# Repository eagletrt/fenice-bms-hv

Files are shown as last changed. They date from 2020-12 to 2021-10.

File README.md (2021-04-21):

# Fenice BMS - hardware

## Libraries
The projects don't include the libraries since they use the KiCAD official ones.
Set accordingly the variables `${KICAD_SYMBOL_DIR}` and `${KISYSMOD}` for 
`kicad-symbols` and `kicad-footprints` respectively.
**For `kicad-symbols` checkout the repo to `v5` for now to have the legacy ones.**

Don't rescue symbols!

## Repo structure
```
fenice-bms-hv:hw-master
|-- docs/       # Docs and datasheets of common interest
|-- mainboard/  # MainBoard hardware project folder
|-- cellboard/  # CellBoard hardware project folder
```

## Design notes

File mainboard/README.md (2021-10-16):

# MainBoard
Formula SAE - unitn

## Authors
Latest first:
- Filippo Volpe
- Franco Tabarelli
- Not clear

## Project structure
```
mainboard/
|-- MainBoard.pro           # Project file
|-- MainBoard.sch           # Schematic root
|-- MainShutdown.sch        # Analog shutdown logic schematic
|-- MCU.sch                 # MCU schematic
|-- HVSide.sch              # High voltage monitoring schematic
|-- MainBoard.kicad_pcb     # Board layout file
|-- MainBoard-cache.lib     # Local cache of symbols
|-- fp-info-cache           # Cache of footprints
|-- fp-lib-table            # List of footprint lib files
|-- sym-lib-table           # List of symbols lib files
|-- gerber/                 # Gerbers outputs
|-- netlists/               # Netlists outputs
|-- images/                 # Board renders and such
|-- docs/                   # Additional related documents and outputs
|   |-- hv-bms-mainboard.md # Report/documentation
|-- bom/                    # BOM folder
```

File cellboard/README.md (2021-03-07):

# CELLBOARD
Formula SAE - unitn

## Authors
Latest first:  
- Francesco Osti v2.1.4  
- Franco Tabarelli v2.0 - 2.1.3  
- Gregor Gombač v0 -   

## Version 2.1.4
Compared to last version we now use NTC termistor to monitor temperature and no longer use digital temperature sensors mounted on flexible PCB

## Project structure
```
cellboard
|-- CellsBoard.pro                    # Project file
|-- CellsBoard.sch                    # Cellboard main schematic
|-- PowerSupply.sch                   # Power sources schematic
|-- Balance.sch                       # Balancer schematic
|-- temperatureADC.sch                # Temperature measurement schematic
|-- Temperature section.sch           # STM microcontroller schematic
|-- LTC6813-1.sch                     # Cell voltage monitor IC schematic
|-- CellsBoard.kicad_pcb              # PCB
|-- CellsBoard-cache.lib              # Local cache of symbols        
|-- CellsBoard.net                    # Netlist
|-- CellsBoard-rescue.dcm             # Component library stuff
|-- CellsBoard-rescue.lib             # Component library stuff
|-- fp-info-cache                     # Cache of footprints
|-- fp-lib-table                      # List of footprint lib files
|-- sym-lib-table                     # List of symbols lib files
|-- modules/                          # Local symbol library files
|   |-- CellsBoard.pretty/            # Local footprint library files
|   |-- logo.kicad_mod/               # Logos fotprints
|   |-- packages3d/                   # 3D models
|   |-- simbolo_E-Agle.pretty/        # Logos E-Agle fotprints
|   |-- simbolo HV/                   # Logos HV fotprints
|-- gerber/                           # Gerber outputs
|-- library/                          # Local symbol library files
```

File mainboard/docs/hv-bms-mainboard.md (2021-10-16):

# Mainboard BMS

The goal has been creating a solid design that I hope will be carried forward with only minor adaptiations to the following team cars.

## Connections
-

## Feedbacks
What to feedback:

- SD_IN
- SD_OUT
- SD_END (no mux)
- SD_RELAY_D (no mux)
- TSAL
- AIR+_STATUS
- AIR-_STATUS
- AIR+_GATE
- AIR-_GATE
- TS_ON
- IMD_FAULT (no mux)
- IMD_LATCHED
- BMS_LATCHED
- EXT_LATCHED
- EXT_FAULT
- TS_OVER_60V_STATUS
- PRECHARGE_STATUS
- MUX_CHECK

The feedbacks are stepped down from the $12V$ logic to the $3.3V$ of the microcontroller. The signals, unless specified above, are the fed to a multiplexer CD74HC4067SM.

## TS side
### Buffers

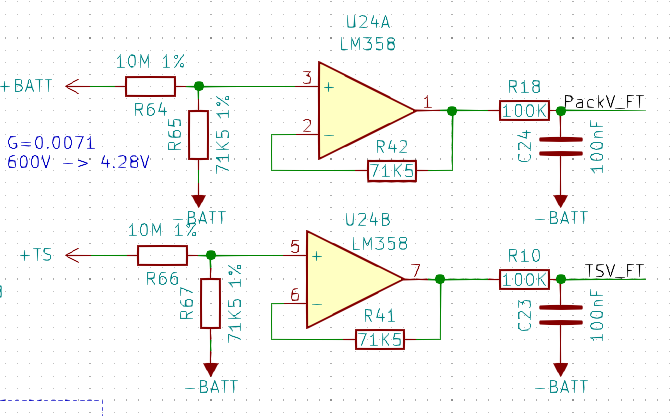
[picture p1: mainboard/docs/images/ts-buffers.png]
HV buffers


To feed the TS voltage into the ADC we use a voltage divider with the values in the image.

The OPAMP used as buffers are standard LM358, the main characteristics we are interested in are:
- Input bias current: $I_b = 45 nA$
- Output saturation voltage: $V_{OH} = V_{cc} - 1.5V = 3.5V$
The first limits the maximum value the voltage divider resistors can have, and with $R_{65} = 10M$ the current is $6uA$ at $60V$ still factor of $100$ more than $I_b$.
The second sets the maximum voltage to be buffered and in our case it's $3.2V$ at $V_{BATT} = 450V$ with some margin to limit non-linearities in the OPAMP and use an ADC at $V_{REF} = 3.3V$.

The gain is thus:
$G = \frac{R_{65}}{R_{65}+R_{64}} \approx 0.0071$

On the feedback line a resistor equal to the output impedence of the divider (hence equal to the lower resistor) is placed to remove the input bias current offset contribution at first order.

The filter cutoff frequency is:
$\omega_LP = \frac{1}{R_{18} C_{24}} = 100 rad/s \ (~16Hz)$

### ADC
Requirements:
- >= 3channels
- > 10bit
- ~ 500kbps
- Visolation > 1800V
- > 10 conversion per second
- < 10us of conversion time

The choice of the ADC was carried out taking into account the availability of the current market, previously the Si8900 IC was employed but it's no more in stock.
```{note}
The Si8900 was great because it integrated in an single package a 10bit SAR ADC and an isolation layer for the UART communication thus reducing BOM entries, space and microcontroller connections.
```

Wanting now to have a more future proof choice it has been decided to switch to a more standard configuration of separated ADC and isolation. UART devices are not common and I2C is more complex to isolate (but doable with a MAX14850). The most widespread ADCs are SPI and is simple to isolate eventhough it requires more lanes
The supply of the ADC is setted to 3.3V since the buffering OPAMP is powered from 5V and saturates.
The configuration choosen is:
- ADC124S021
	- 4 channels
	- 12bit
	- 200kbps
	- R series MUX 500Ohm
	- 50pF hold capacitance
	- 3.3V compatible

- MAX2245
- MAX2246
	- 3.3V compatible
	- 200Mbps
	- 5kV isolationwithstand

The ADC is then connected to the SPI1 on the microcontroller.

## Fan control

From TIM3_CH1 of the microcontroller put out a 25kHz PWM to control the fans.
The power for the fans is not routed to the mainboard, GND and +12V goes from the connector to the fan with a series fuse TBD on the 12V line.

## Buzzer

The buzzer is used to signal an urgency inside the TSAC.
Such emergencies are:
- Inconsistencies between control and feedbacks on the AIRs
- Prolungated overtemperature
- Fan failure

## CAN

The CAN transceiver for the communication with the outside of the TSAC is the MCP2562 which is also used in the rest of the vehicle. The termination resistor has the place to be soldered but of course it's only necessary at the end of the bus so it can be soldered in one pad only and orientated away from the other pad.

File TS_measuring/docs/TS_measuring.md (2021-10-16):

# TS_measuring

This board is meant to deal with the voltage indicator and TS voltage measuring for the TSAL control.

## Power

Power mainly comes into the board from the BMS mainboard but to comply with rule EV 5.4.10(FSG2022) it must work also when the LVS is disconnected. To achieve this a linear regulator is implemented that steps down the TS voltage to a menageable value and when the LVS is connected the regulator is for the most part disabled and power comes from the LVS for less heat production.

### Linear regulator

We opted to not use a switching regulator because the input voltage can vary an order of magnitude and would cause a regulator to be unreliable on such a wide span of possible duty cycles so a simple linear regulator is preferred.
The circuit is a classic discrete components linear regulator with the main dissipation components being a nmos DMN80H2D0SCTI capable of sustaining a Vds of 800V. The feedback works around the 0.6V of the forward bias of the base of NPN transistor Q1.

$$
	V_{out} = V_{FB} \frac{R_2+R_3}{R_3} \\
	R_2=R_3 (\frac{V_{out}-V_{FB}}{VV_{FB}})
$$

The feedback networks choice is then:
- R2 = $150k\Omega$
- R3 = $10k\Omega$

### LVS bypass

When the LVS is connected and powered the linear regulator is bypassed by the ORing and it's turned off the linreg leaving only power wasted into R1:

$$
	P_{R1,max} = \frac{(600V)^2}{R1}=0.36W
$$

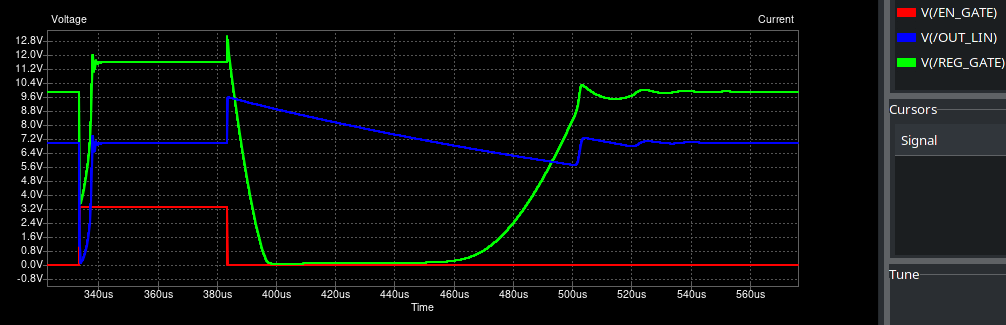
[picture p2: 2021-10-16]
TS_measuring/docs/images/output_short_regulation.png

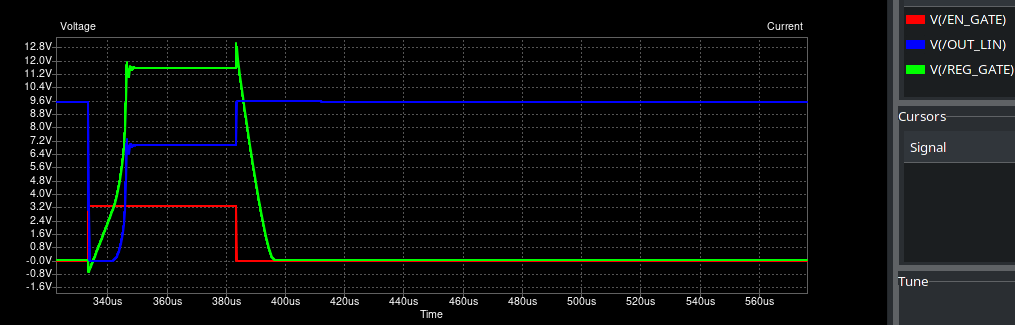
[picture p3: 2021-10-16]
TS_measuring/docs/images/output_short_to_open_regulation.png

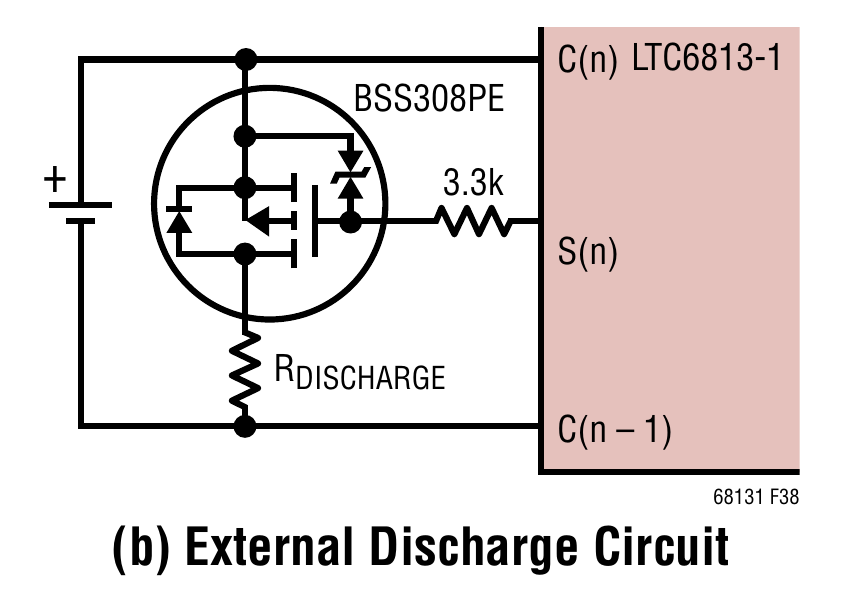
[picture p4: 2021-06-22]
cellboard/docs/images/LTC6813_cell_connection.png

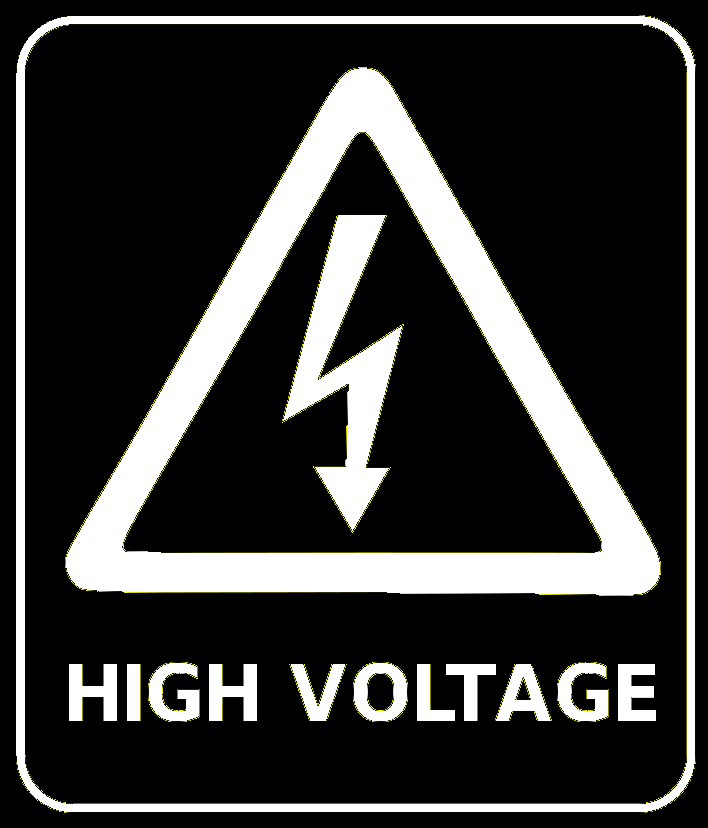
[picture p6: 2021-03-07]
cellboard/modules/simbolo HV/hv_colo.png

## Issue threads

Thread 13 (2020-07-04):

Current measurement

Bonnee, 2020-07-04:
Implement formula reading from current sensors, with some way to switch between sensors when a current threshold is reached

Bonnee, 2021-09-25:
Mostly fixed by 0509a0651be2edcbd3b963c28a7c65b585f54e12

Closed 2021-09-25.

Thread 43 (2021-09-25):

EEPROM doesn't work

Bonnee, 2021-09-25:
On the latest F4 board, communication with the on-board EEPROM is broken. It might be a driver issue, but as far as I remember the driver worked on the G4 board. @volpx please check that nothing changed on the EEPROM circuit.

volpx, 2021-10-02:
Doesn't answer to SPI commands, always returns 0xFF.

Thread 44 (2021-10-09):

ADC1 in DMA mode doesn't work

Bonnee, 2021-10-09:
Starting ADC1 in DMA mode does only one conversion and then stops. Read values seem to overflow at 255, meaning only 8 bits are used. Should not be a problem since ADC2 and ADC3 are used to measure current and the feedbacks can only be read in polling mode since they are multiplexed

volpx, 2021-10-10:
The multiplexer is not the reason the feedbacks can't be DMAed. You can probably do it but the reason is it's not necessary to have them DMAed.

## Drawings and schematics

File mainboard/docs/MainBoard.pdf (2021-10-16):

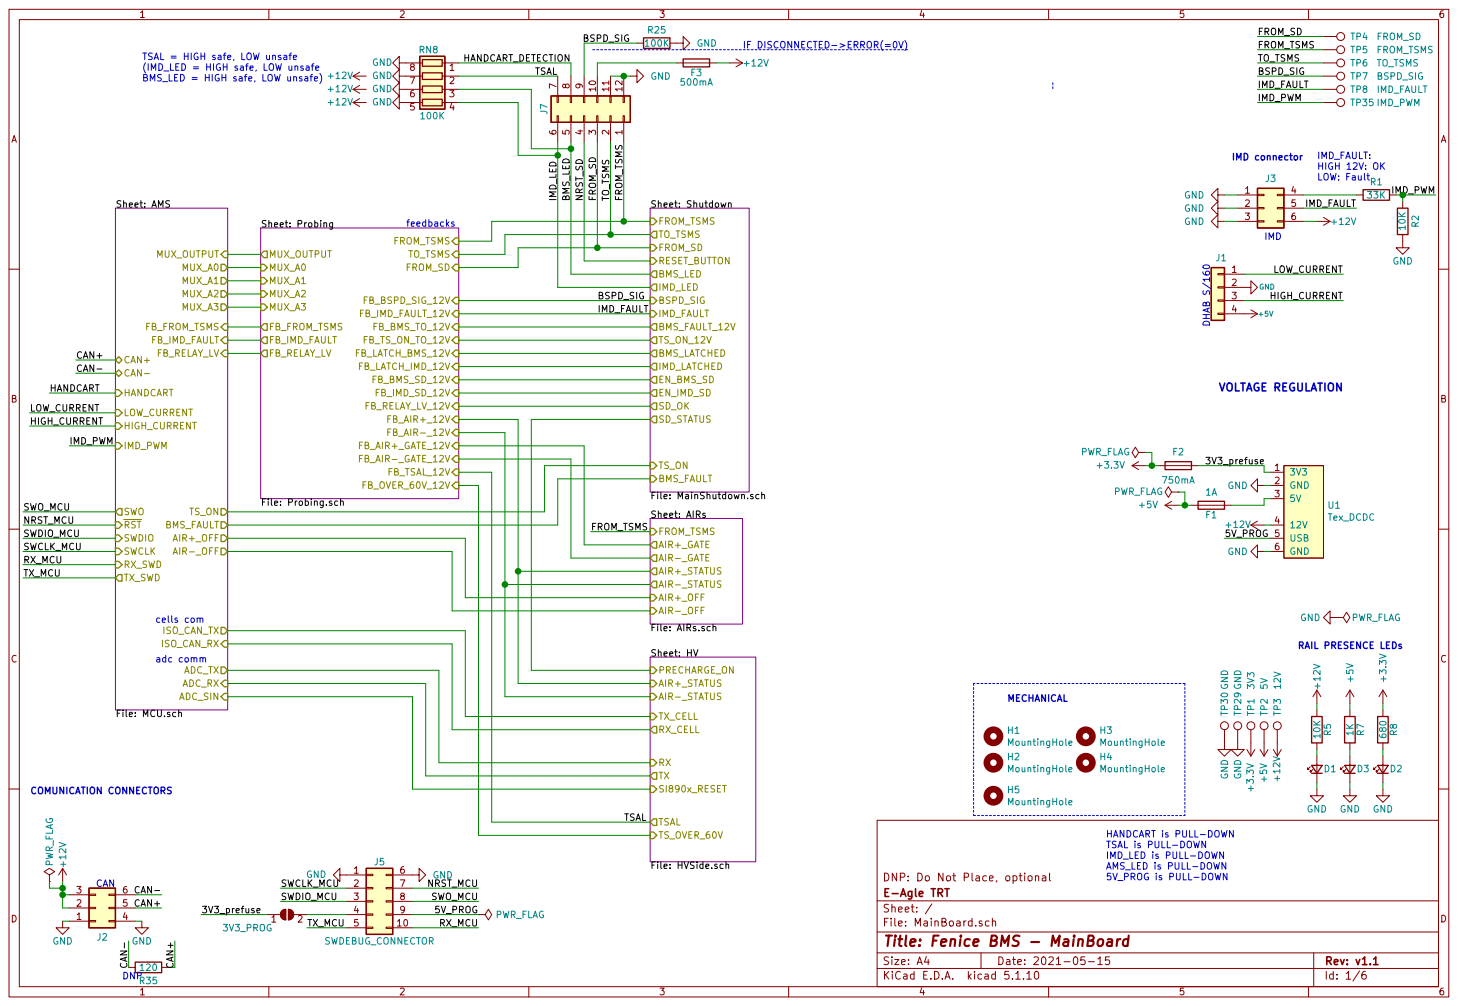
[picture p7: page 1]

LOW: Fault TSAL = HIGH safe, LOW unsafe
(IMD_LED = HIGH safe, LOW unsafe

IF DISCONNECTED->ERROR(=0V)
Sheet: Shutdown File: MainShutdown.sch TS_ON

AIR+_STATUS
AIR-_STATUS
AIR-_OFF AIR+_OFF Sheet: HV
File: HVSide.sch AIR-_STATUS
TXRX_CELL TX_CELL SI890x_RESET

TSAL is PULL-DOWN
IMD_LED is PULL-DOWN
AMS_LED is PULL-DOWN
5V_PROG is PULL-DOWN

DNP: Do Not Place, optional
File: MainBoard.sch Sheet: / E-Agle TRT

Id: 1/6 Title: Fenice BMS - MainBoard

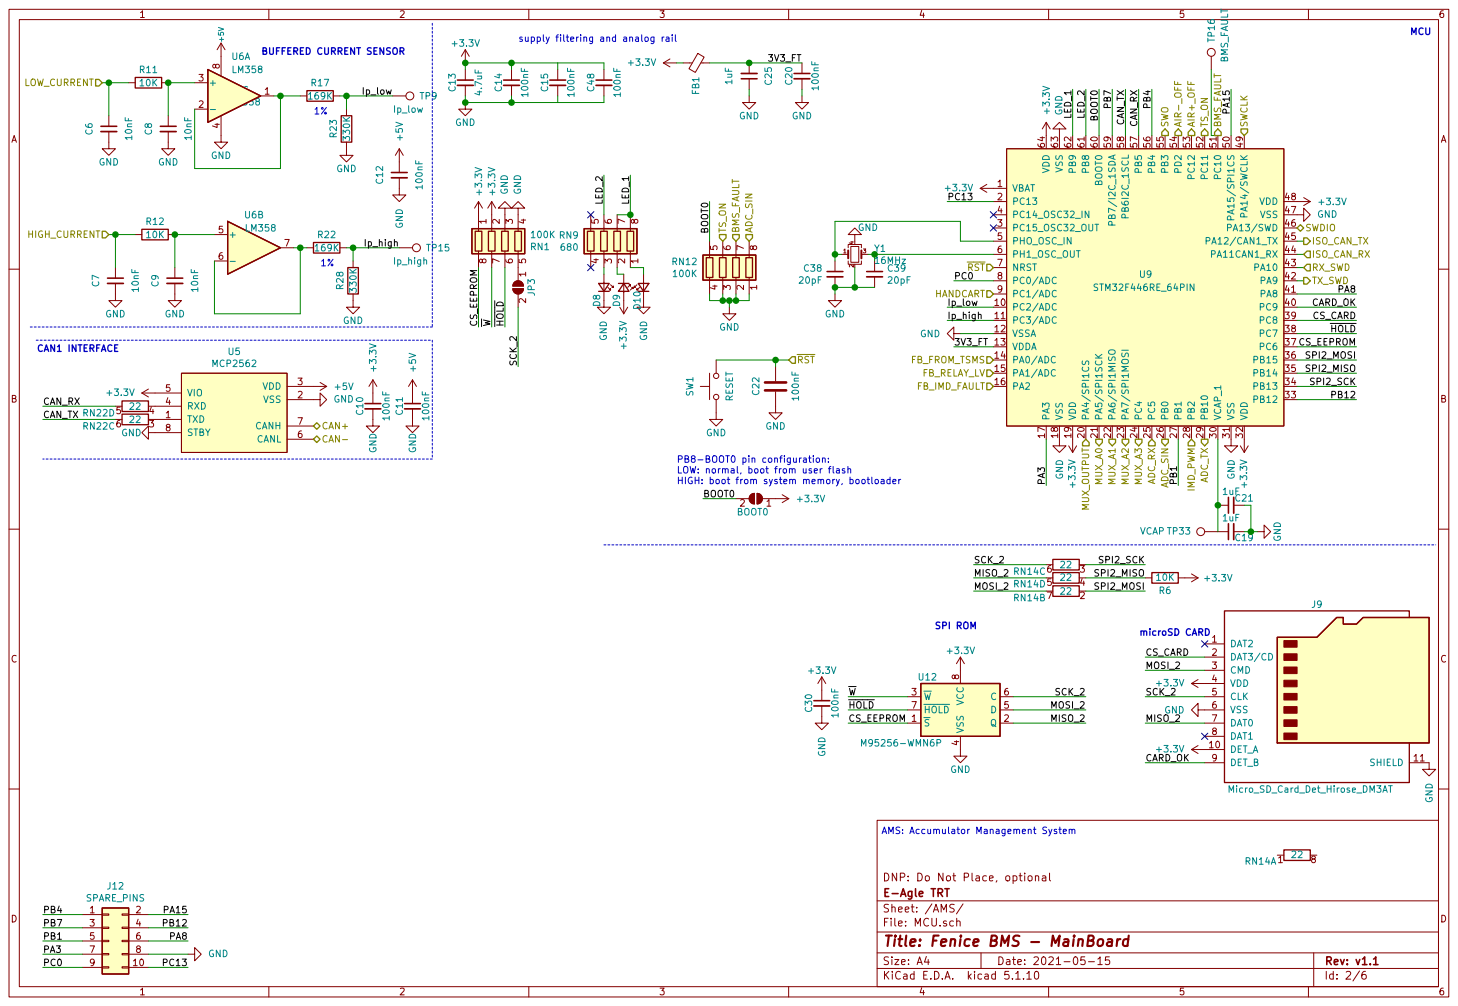
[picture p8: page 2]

supply filtering and analog rail

AMS: Accumulator Management System

DNP: Do Not Place, optional
File: MCU.sch Sheet: /AMS/ E-Agle TRT

Id: 2/6 Title: Fenice BMS - MainBoard

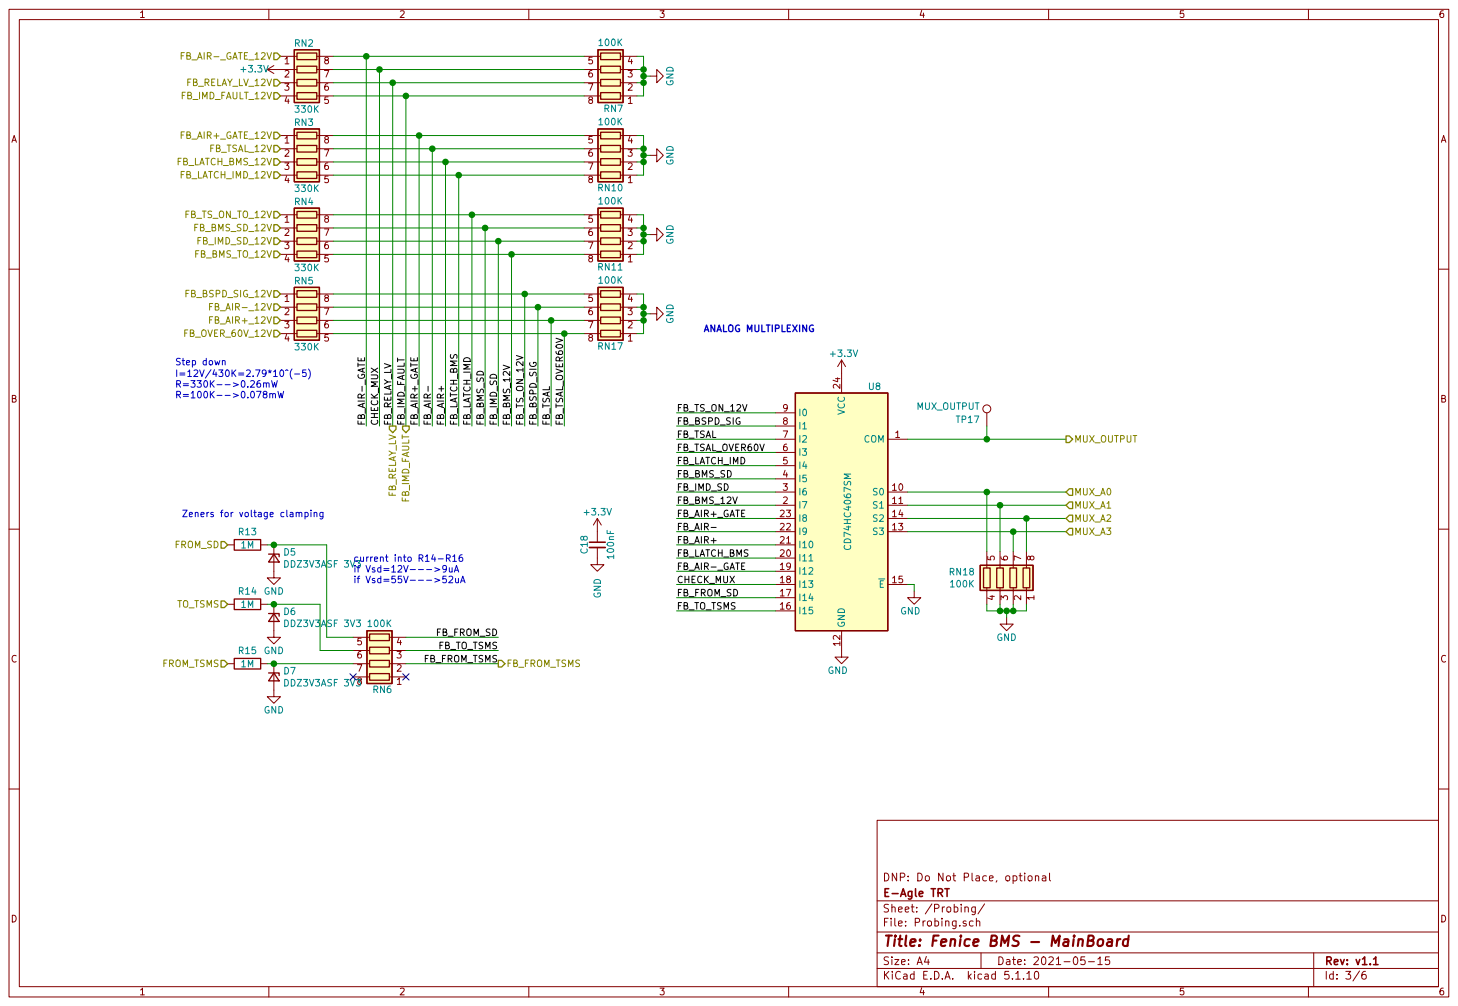
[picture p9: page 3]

Zeners for voltage clamping

DNP: Do Not Place, optional GND

E-Agle TRT
Sheet: /Probing/
File: Probing.sch
Id: 3/6 Title: Fenice BMS - MainBoard

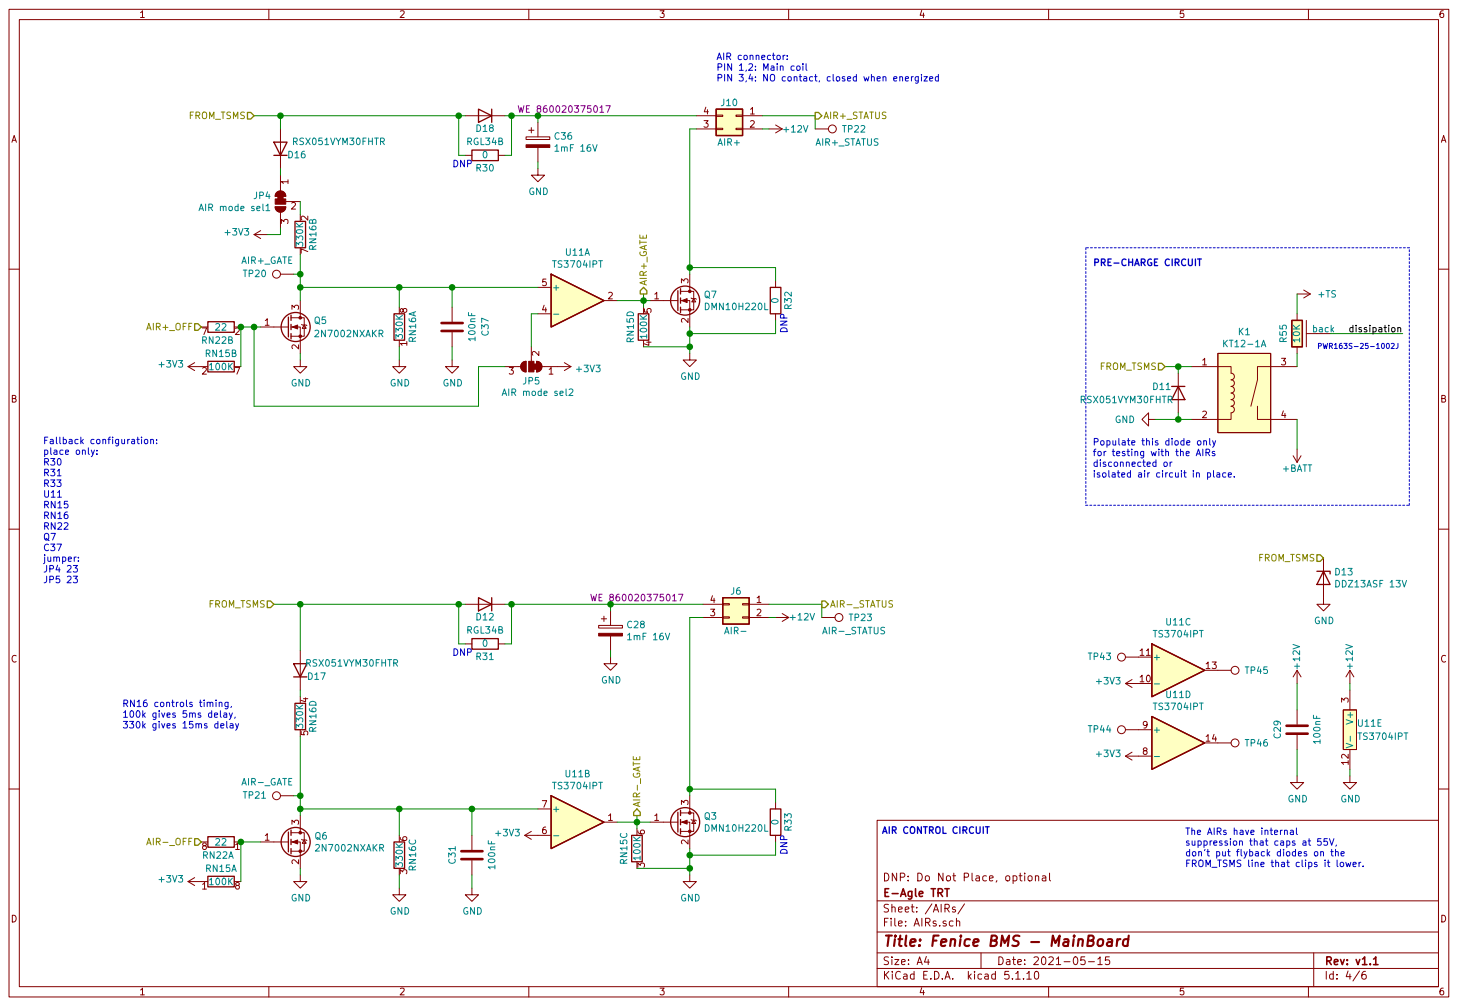
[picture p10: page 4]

AIR connector: PIN 1,2: Main coil PIN 3,4: NO contact, closed when energized

PWR163S-25-1002J Populate this diode only
FROM_TSMS

for testing with the AIRs disconnected or

isolated air circuit in place. DNP

AIR CONTROL CIRCUIT DNP

The AIRs have internal suppression that caps at 55V,

don't put flyback diodes on the
FROM_TSMS line that clips it lower.

DNP: Do Not Place, optional
File: AIRs.sch Sheet: /AIRs/ E-Agle TRT

Id: 4/6 Title: Fenice BMS - MainBoard

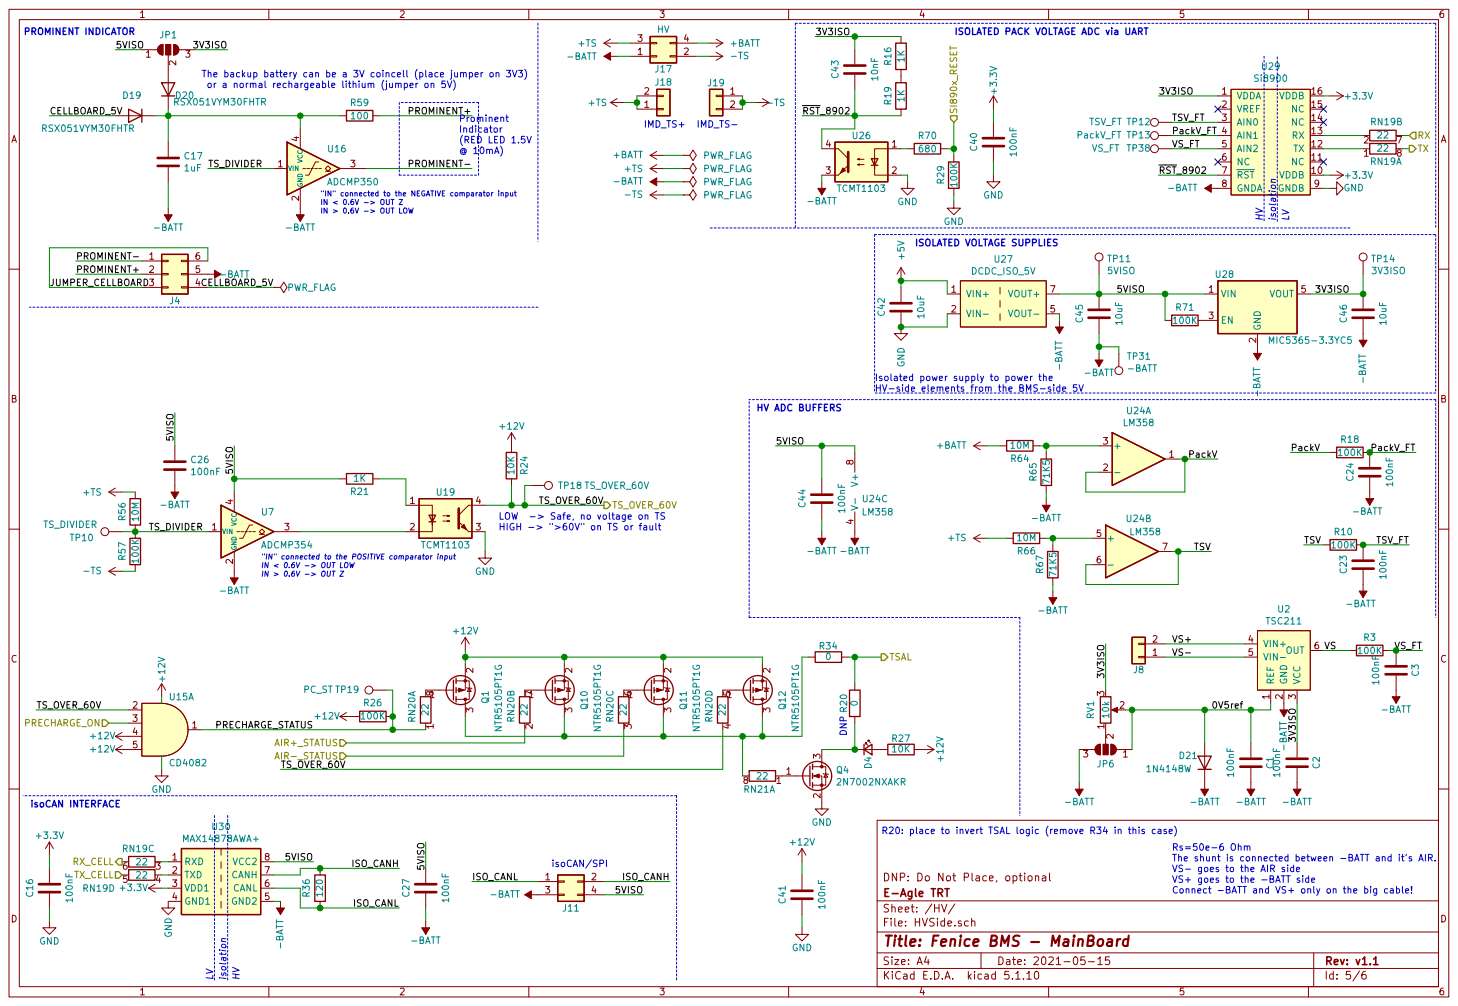
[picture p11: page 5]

3V3ISO
The backup battery can be a 3V coincell (place jumper on 3V3)
or a normal rechargeable lithium (jumper on 5V)

"IN" connected to the NEGATIVE comparator input
IN < 0.6V -> OUT Z
IN > 0.6V -> OUT LOW

LOW -> Safe, no voltage on TS HIGH -> ">60V" on TS or fault

"IN" connected to the POSITIVE comparator input
IN < 0.6V -> OUT LOW
IN > 0.6V -> OUT Z

3 VIN+ 4 VIN- 5 OUT 6 U2 TSC211 -BATT3 6 RN20C 22 C2 100nF -BATT C3 100nF -BATT C1 100nF -BATT

DNP: Do Not Place, optional R26

R20: place to invert TSAL logic (remove R34 in this case)

The shunt is connected between -BATT and it's AIR. VS- goes to the AIR side

File: HVSide.sch Sheet: /HV/ E-Agle TRT

VS+ goes to the -BATT side

Id: 5/6 Title: Fenice BMS - MainBoard

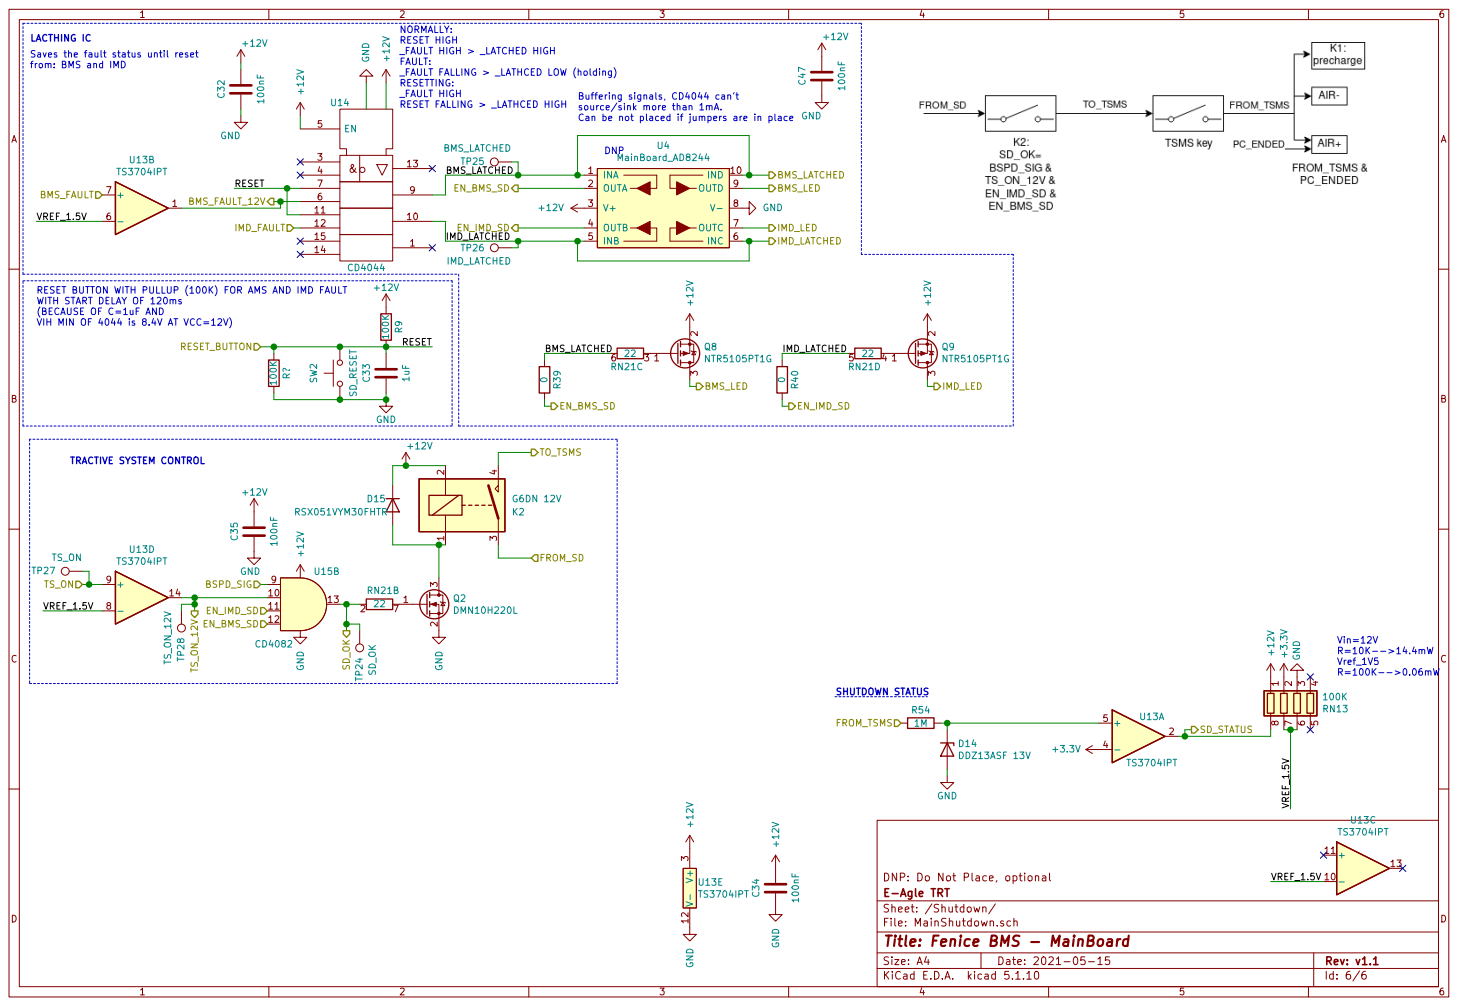
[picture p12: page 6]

LACTHING IC
Saves the fault status until reset
from: BMS and IMD

RESET NORMALLY: RESET HIGH
RESET

_FAULT HIGH > _LATCHED HIGH
FAULT: _FAULT FALLING > _LATHCED LOW (holding) RESETTING: _FAULT HIGH

Buffering signals, CD4044 can't source/sink more than 1mA. Can be not placed if jumpers are in place DNP

RESET BUTTON WITH PULLUP (100K) FOR AMS AND IMD FAULT WITH START DELAY OF 120ms (BECAUSE OF C=1uF AND

DNP: Do Not Place, optional R9 100K TP24 SD_OK +12V

VIH MIN OF 4044 is 8.4V AT VCC=12V)

File: MainShutdown.sch Sheet: /Shutdown/ E-Agle TRT

Id: 6/6 Title: Fenice BMS - MainBoard

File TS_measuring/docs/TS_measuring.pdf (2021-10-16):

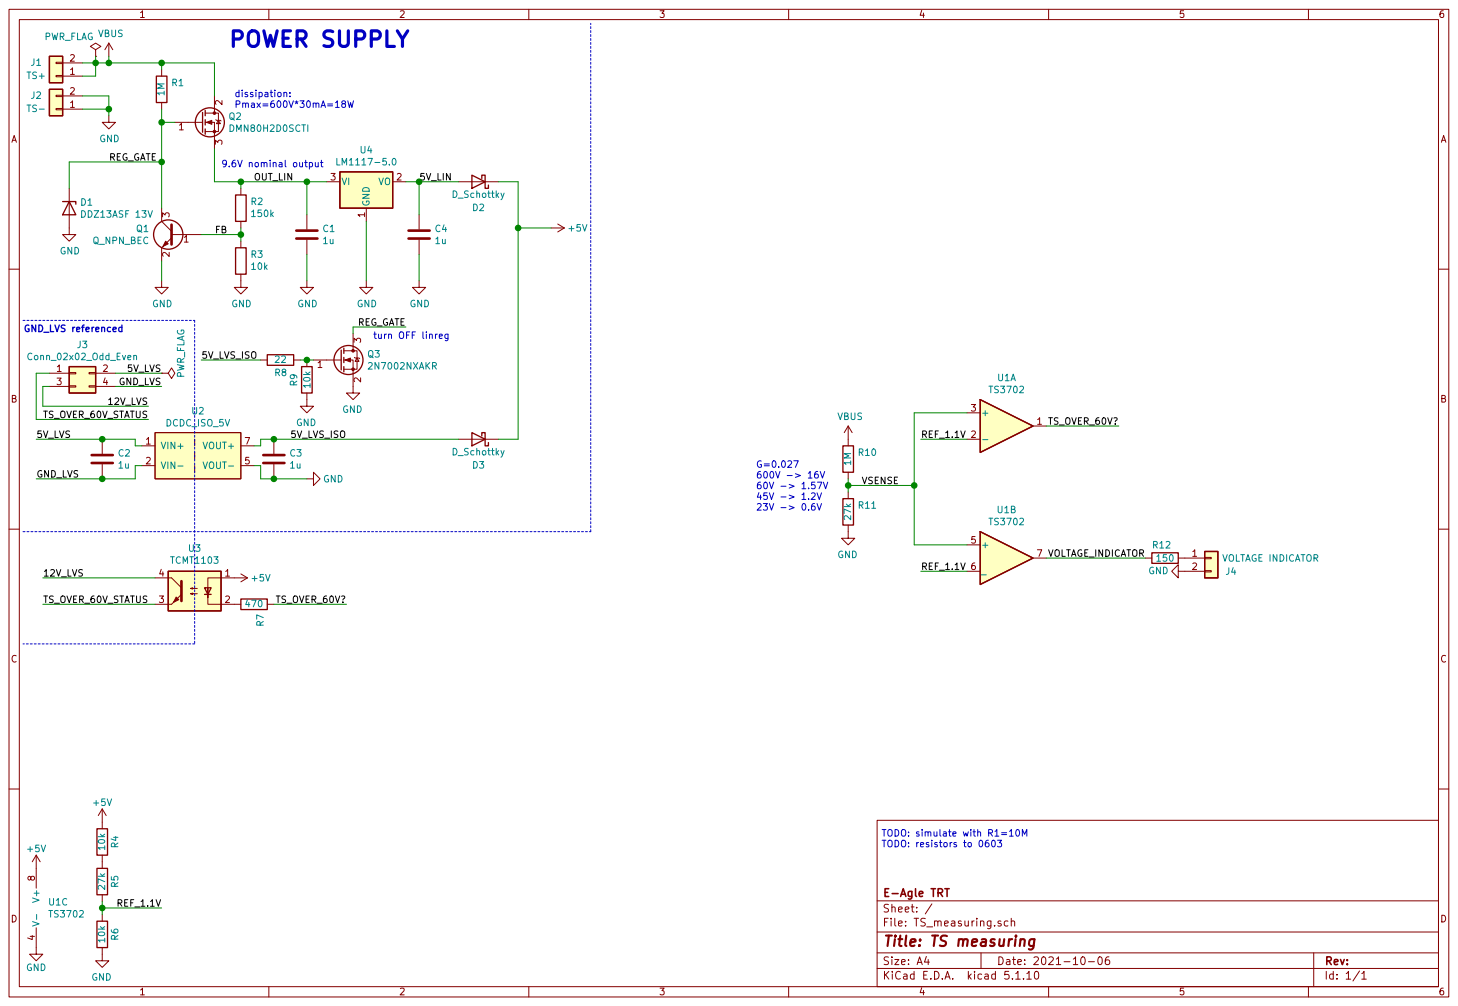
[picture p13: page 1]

File: TS_measuring.sch Sheet: / E-Agle TRT GND

Id: 1/1 Title: TS measuring

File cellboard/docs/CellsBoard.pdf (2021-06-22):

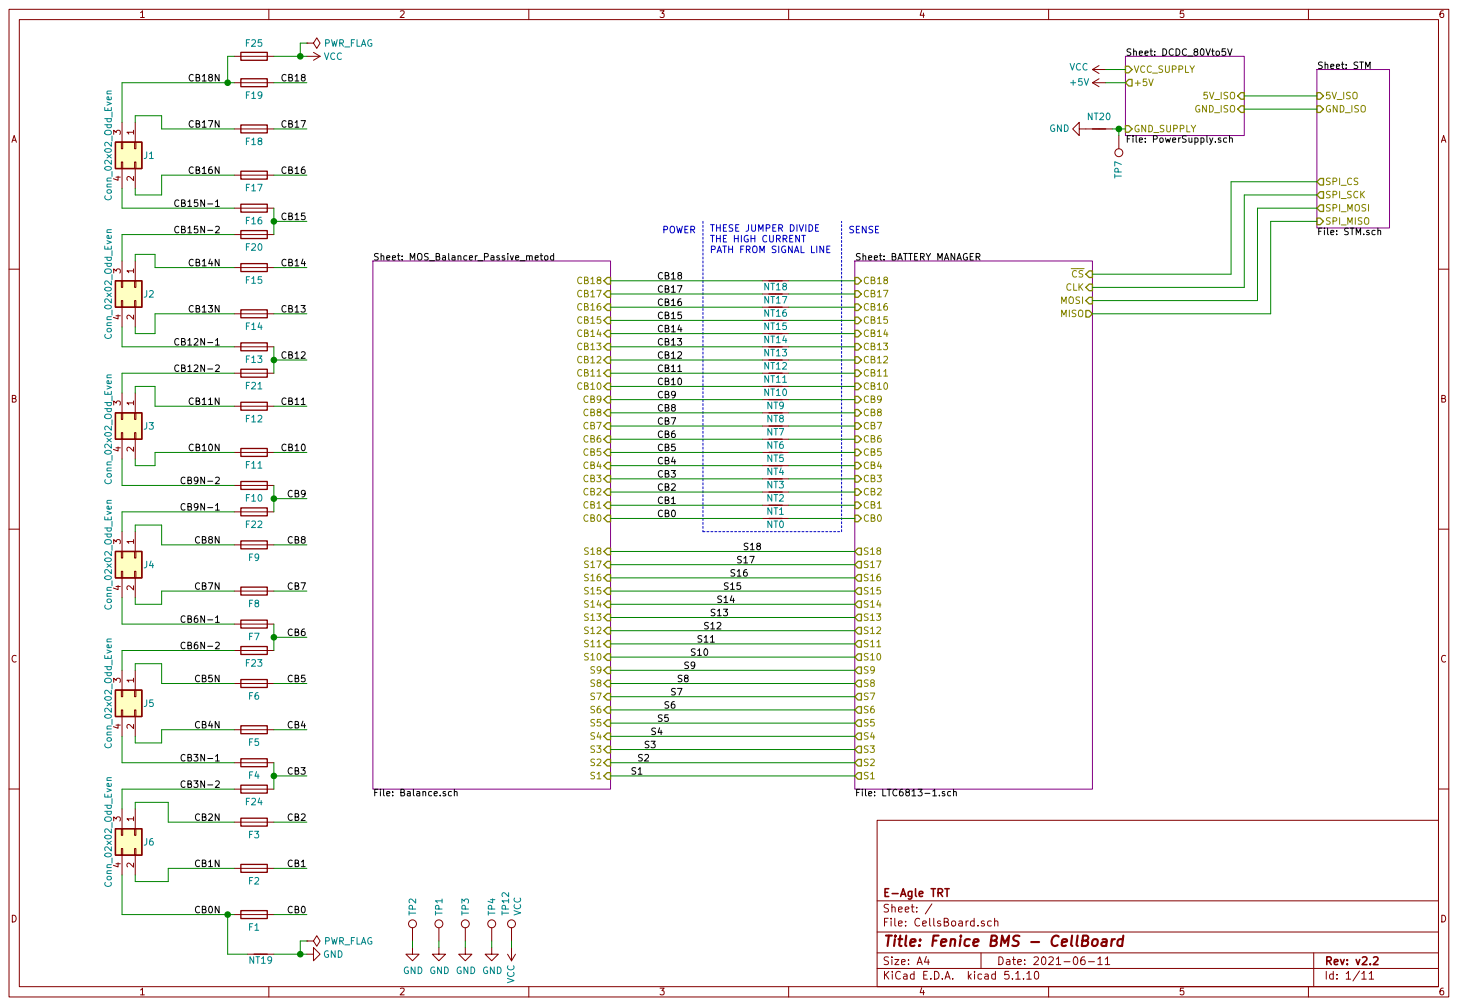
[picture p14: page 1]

THESE JUMPER DIVIDE
THE HIGH CURRENT PATH FROM SIGNAL LINE

File: CellsBoard.sch Sheet: / E-Agle TRT

Id: 1/11 Title: Fenice BMS - CellBoard

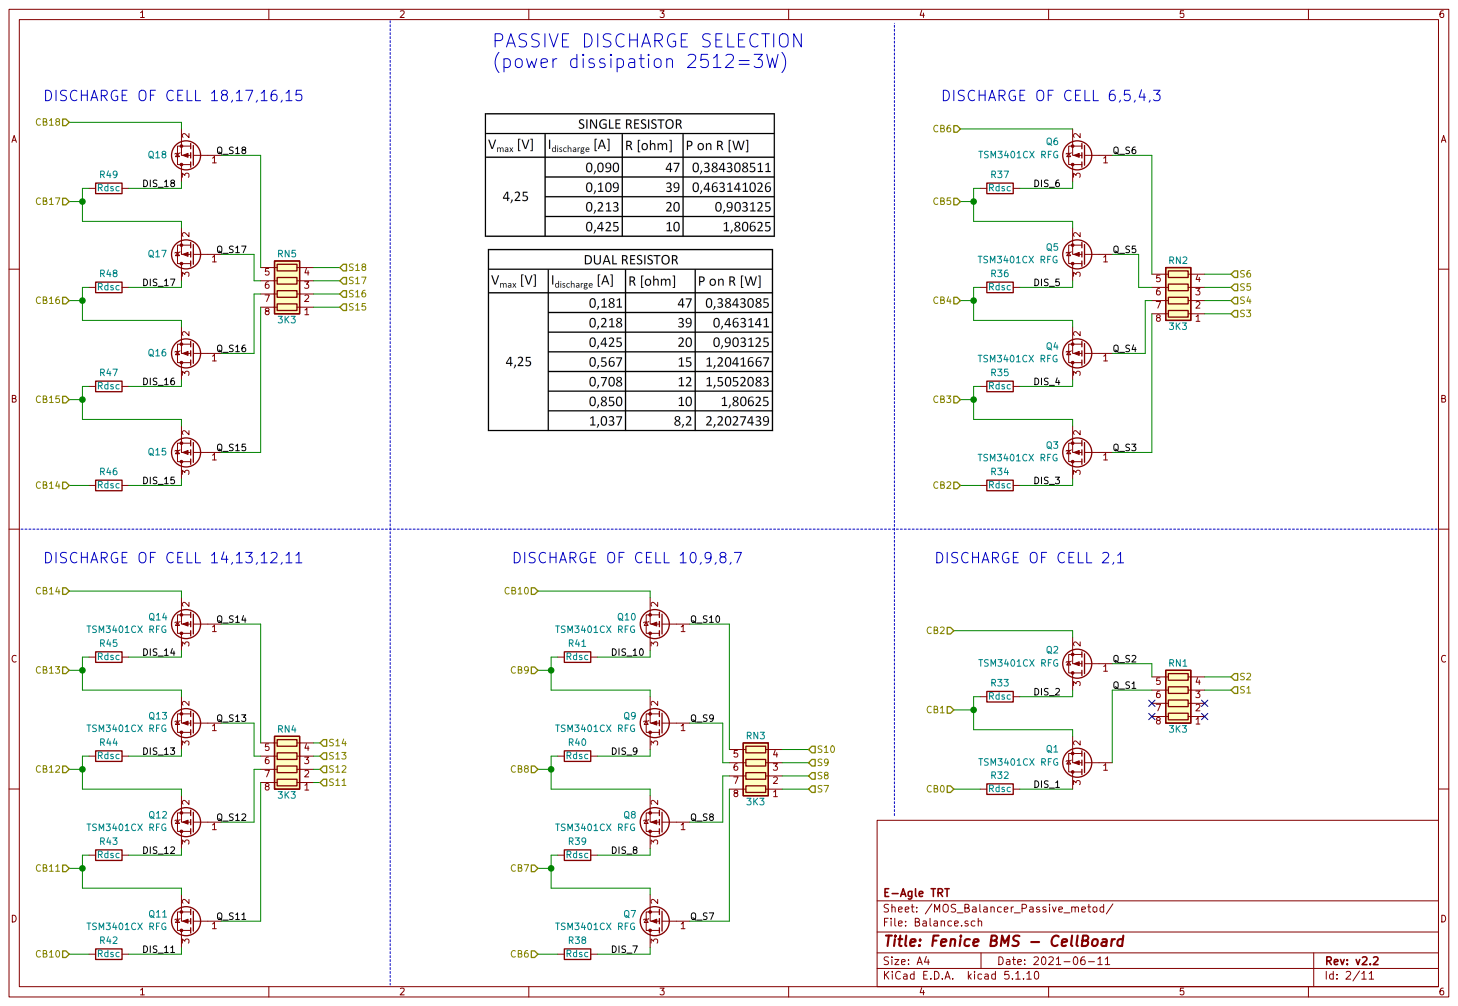
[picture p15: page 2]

E-Agle TRT
File: Balance.sch Sheet: /MOS_Balancer_Passive_metod/
Id: 2/11 Title: Fenice BMS - CellBoard

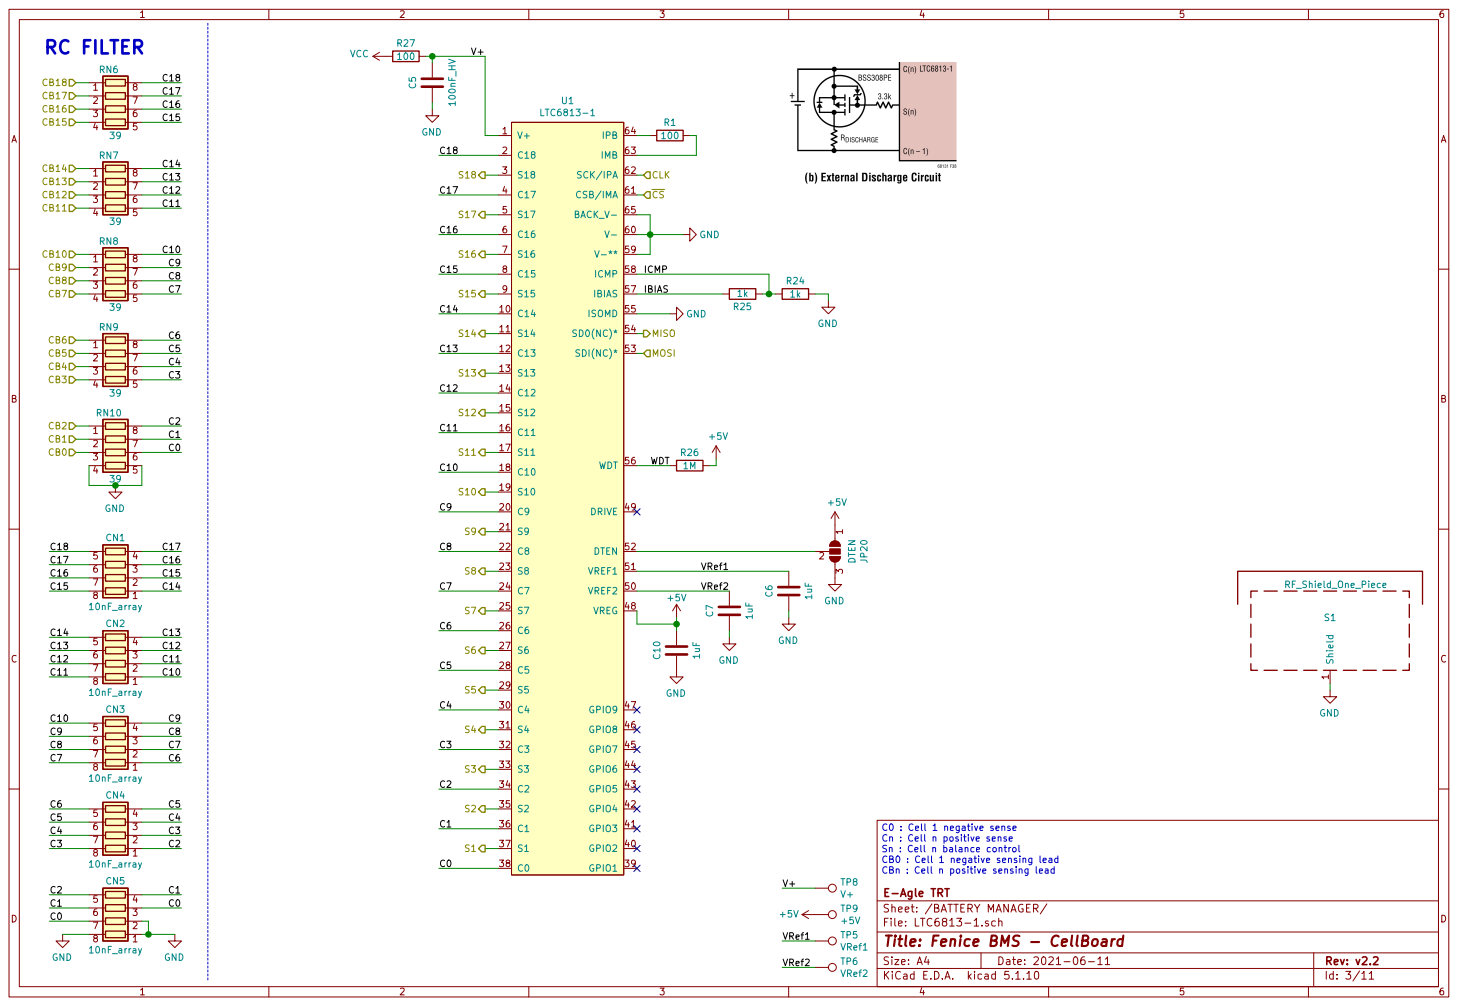
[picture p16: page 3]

C0 : Cell 1 negative sense
Cn : Cell n positive sense Sn : Cell n balance control CB0 : Cell 1 negative sensing lead

CBn : Cell n positive sensing lead

TP5 VRef1 TP6 VRef2
Id: 3/11 Title: Fenice BMS - CellBoard

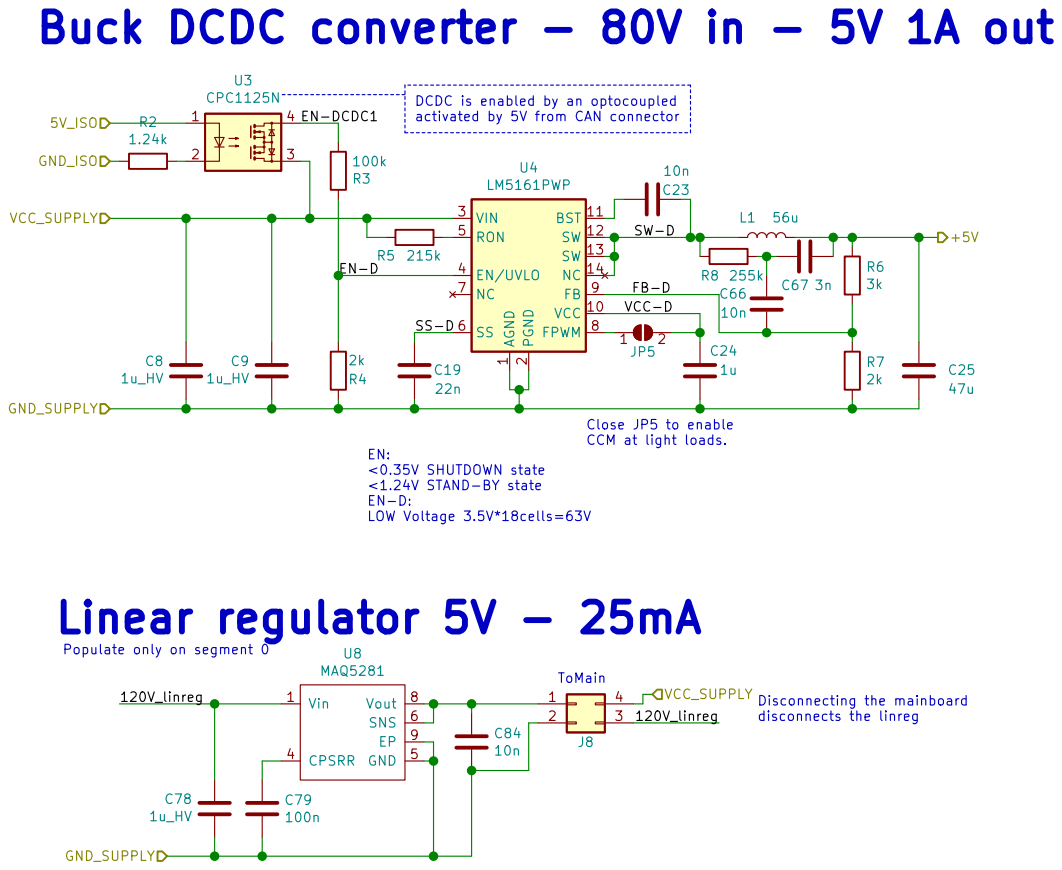
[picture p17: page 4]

Buck DCDC converter - 80V in - 5V 1A out

activated by 5V from CAN connector Close JP5 to enable CCM at light loads. ToMain Populate only on segment 0
5V_ISO

2 VIN 3 EN/UVLO 4 RON 5 SS 6 NC 7 FPWM 8 FB 9 U4
120V_linreg SW-D
10n VCC_SUPPLY

1 VCC 10 BST 11 SW 12 SW 13 NC 14 PGND

disconnects the linreg EN: <0.35V SHUTDOWN state <1.24V STAND-BY state EN-D: LOW Voltage 3.5V*18cells=63V

E-Agle TRT
Sheet: /DCDC_80Vto5V/
File: PowerSupply.sch
Id: 4/11 Title: Fenice BMS - CellBoard

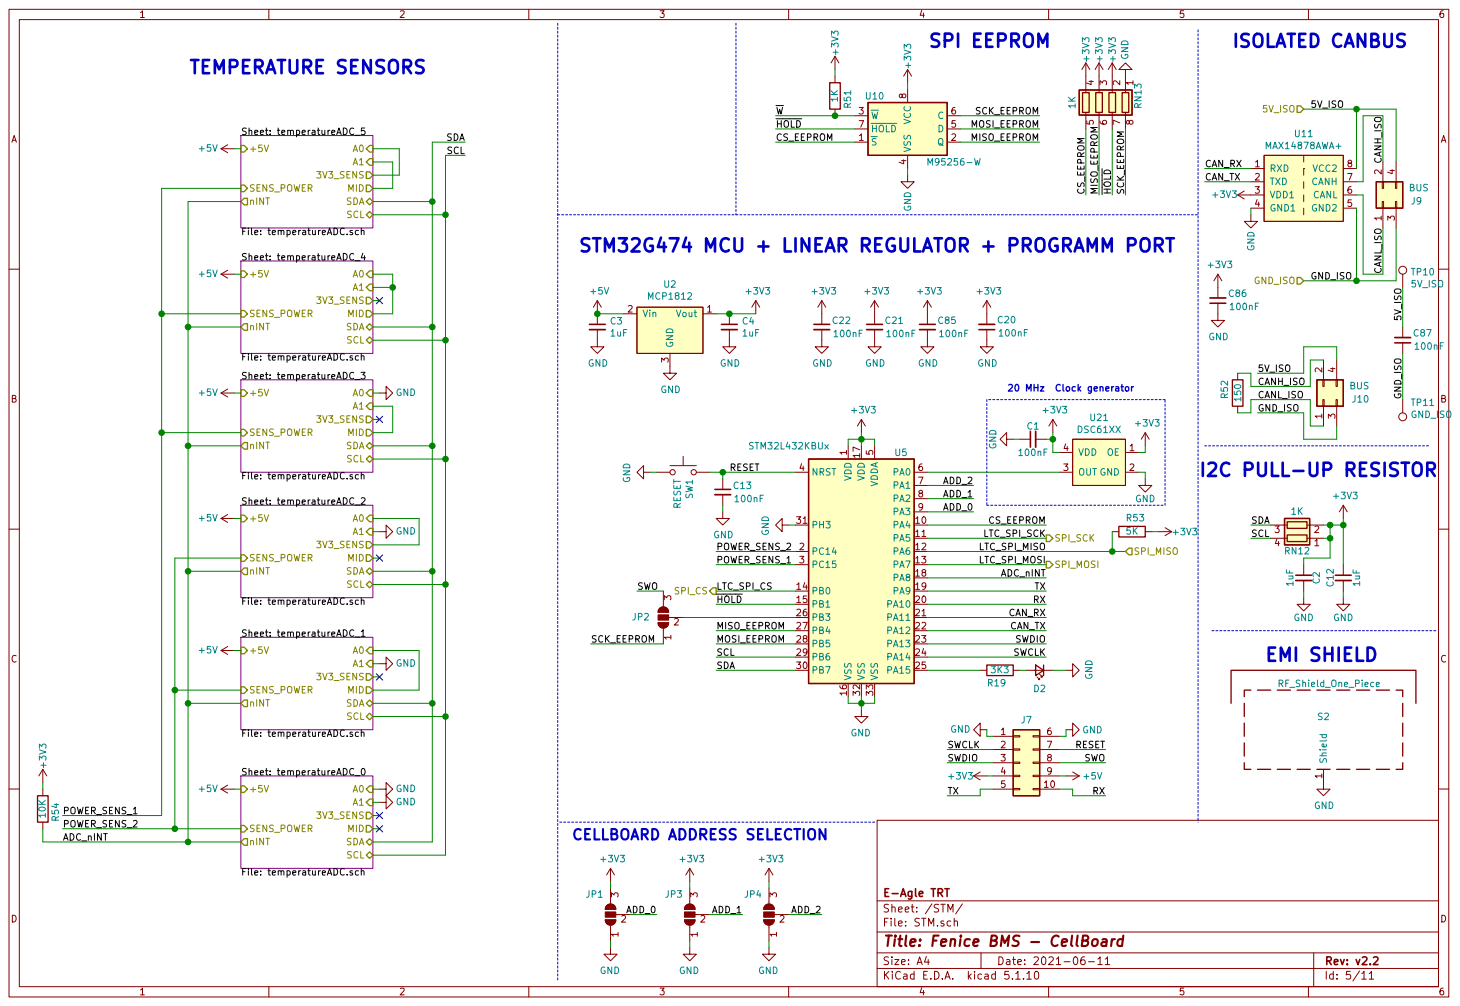
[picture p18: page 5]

STM32G474 MCU + LINEAR REGULATOR + PROGRAMM PORT

5 VSS 16 VSS 32 VSS 33 U5 STM32L432KBUx GND GND

File: STM.sch Sheet: /STM/ E-Agle TRT

Id: 5/11 Title: Fenice BMS - CellBoard


E-Agle TRT
Sheet: /STM/temperatureADC_3/
File: temperatureADC.sch
Id: 6/11 Title: Fenice BMS - CellBoard


E-Agle TRT
Sheet: /STM/temperatureADC_4/
File: temperatureADC.sch
Id: 7/11 Title: Fenice BMS - CellBoard


E-Agle TRT
Sheet: /STM/temperatureADC_1/
File: temperatureADC.sch
Id: 8/11 Title: Fenice BMS - CellBoard


E-Agle TRT
Sheet: /STM/temperatureADC_0/
File: temperatureADC.sch
Id: 9/11 Title: Fenice BMS - CellBoard


E-Agle TRT
Sheet: /STM/temperatureADC_2/
File: temperatureADC.sch
Id: 10/11 Title: Fenice BMS - CellBoard


E-Agle TRT
Sheet: /STM/temperatureADC_5/
File: temperatureADC.sch
Id: 11/11 Title: Fenice BMS - CellBoard





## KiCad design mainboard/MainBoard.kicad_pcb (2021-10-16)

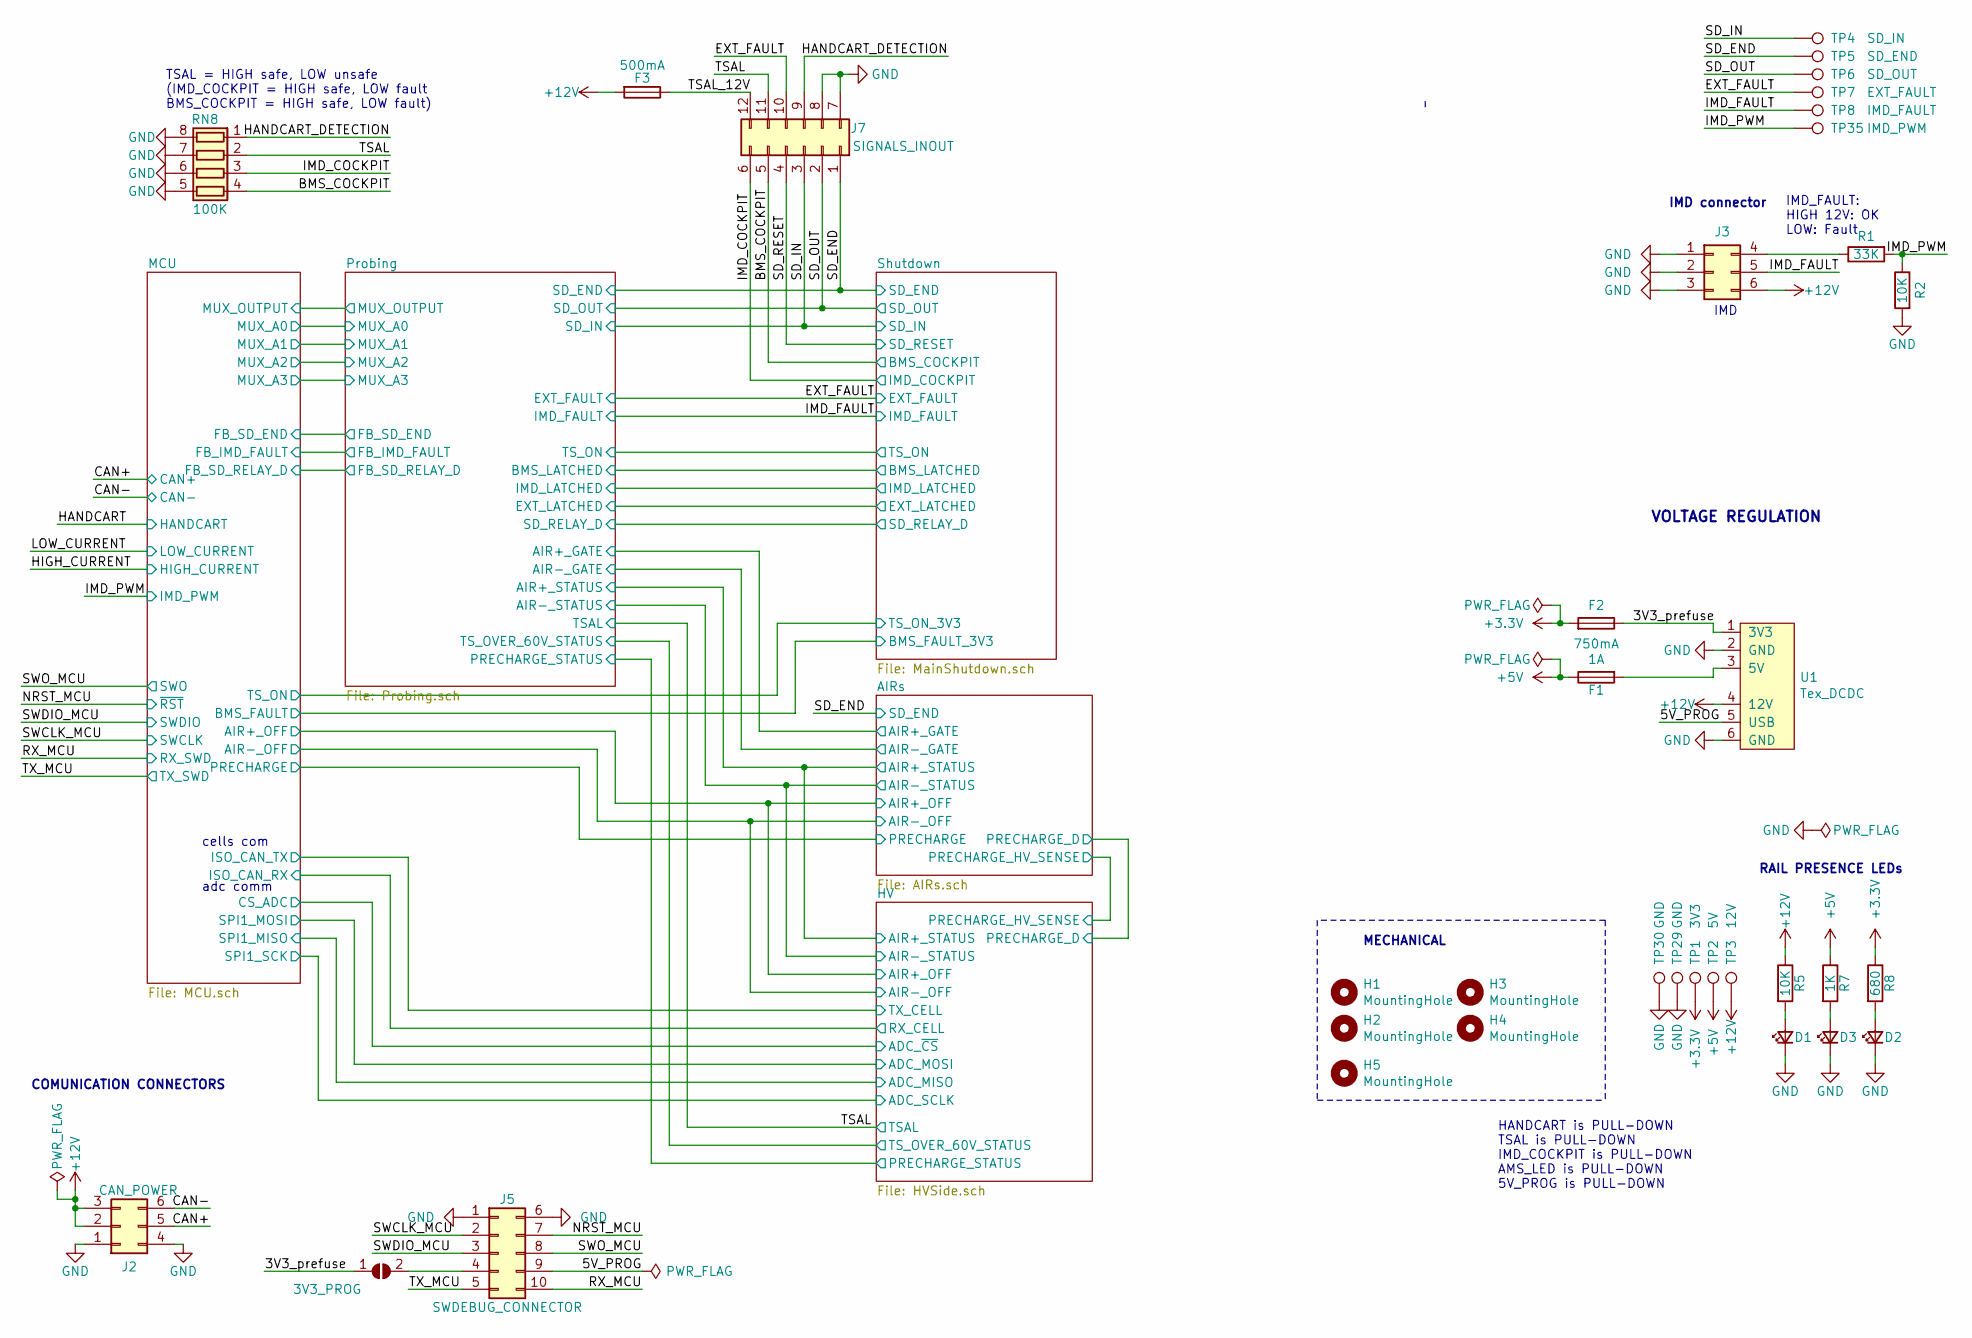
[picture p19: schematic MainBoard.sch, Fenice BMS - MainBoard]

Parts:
D1, D2, D3: LED_Small; LED_0603_1608Metric_Castellated
F1: 1A; Fuse_0805_2012Metric
F2: 750mA; Fuse_0805_2012Metric
F3: 500mA; Fuse_1812_4532Metric
H1, H2, H3, H4, H5: MountingHole; MountingHole_3.2_6.1Free
J2: CAN_POWER; Molex_Micro-Fit_3.0_43045-0612_2x03_P3.00mm_Vertical
J3: CONN_2X3; Molex_Micro-Fit_3.0_43045-0612_2x03_P3.00mm_Vertical
J5: SWDEBUG_CONNECTOR; Molex_Nano-Fit_105310-xx10_2x05_P2.50mm_Vertical
J7: SIGNALS_INOUT; Molex_Micro-Fit_3.0_43045-1212_2x06_P3.00mm_Vertical
JP2: 3V3_PROG; SolderJumper-2_P1.3mm_Open_RoundedPad1.0x1.5mm
R1: 33K; R_0603_1608Metric
R2, R5: 10K; R_0603_1608Metric
R7: 1K; R_0603_1608Metric
R8: 680; R_0603_1608Metric
RN8: 100K; R_Array_Convex_4x0603
TP1: 3V3; TestPoint_Pad_D1.0mm
TP2: 5V; TestPoint_Pad_D1.0mm
TP3: 12V; TestPoint_Pad_D1.0mm
TP4: SD_IN; TestPoint_Pad_D1.0mm
TP5: SD_END; TestPoint_Pad_D1.0mm
TP6: SD_OUT; TestPoint_Pad_D1.0mm
TP7: EXT_FAULT; TestPoint_Pad_D1.0mm
TP8: IMD_FAULT; TestPoint_Pad_D1.0mm
TP29, TP30: GND; TestPoint_GNDedge
TP35: IMD_PWM; TestPoint_Pad_D1.0mm
U1: Tex_DCDC; Tex_DCDC_vertical_up

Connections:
+5V: F1.1, R7.1, TP2.1; also elsewhere on the board
+12V: F3.2, J2.2, J2.3, J3.6, R5.1, TP3.1, U1.4 (12V); also elsewhere on the board
/3V3_prefuse: F2.1, JP2.1 (A), U1.1 (3V3)
/5V_PROG: J5.9, U1.5 (USB)
/BMS_COCKPIT: J7.5, RN8.4 (R4.1); also elsewhere on the board
/CAN+: J2.5; also elsewhere on the board
/CAN-: J2.6; also elsewhere on the board
/EXT_FAULT: J7.10, TP7.1; also elsewhere on the board
/HANDCART_DETECTION: J7.9, RN8.1 (R1.1)
/IMD_COCKPIT: J7.6, RN8.3 (R3.1); also elsewhere on the board
/IMD_FAULT: J3.5, TP8.1; also elsewhere on the board
/IMD_PWM: R1.2, R2.1, TP35.1; also elsewhere on the board
/NRST_MCU: J5.7; also elsewhere on the board
/RX_MCU: J5.10; also elsewhere on the board
/SD_END: J7.1, TP5.1; also elsewhere on the board
/SD_IN: J7.3, TP4.1; also elsewhere on the board
/SD_OUT: J7.2, TP6.1; also elsewhere on the board
/SD_RESET: J7.4; also elsewhere on the board
/SWCLK_MCU: J5.2; also elsewhere on the board
/SWDIO_MCU: J5.3; also elsewhere on the board
/SWO_MCU: J5.8; also elsewhere on the board
/TSAL: J7.11, RN8.2 (R2.1); also elsewhere on the board
/TSAL_12V: F3.1, J7.12
/TX_MCU: J5.5; also elsewhere on the board
GND: D1.1 (K), D2.1 (K), D3.1 (K), J2.1, J2.4, J3.1, J3.2, J3.3, J5.1, J5.6, J7.7, J7.8, R2.2, RN8.5 (R4.2), RN8.6 (R3.2), RN8.7 (R2.2), RN8.8 (R1.2), TP29.1, TP30.1, U1.2 (GND), U1.6 (GND); also elsewhere on the board
unnamed: D1.2 (A), R5.2
unnamed: D2.2 (A), R8.2
unnamed: D3.2 (A), R7.2
unnamed: F1.2, U1.3 (5V)
unnamed: J3.4, R1.1
unnamed: J5.4, JP2.2 (B)

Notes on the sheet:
IMD
IMD connector
COMUNICATION CONNECTORS
MECHANICAL
IMD_FAULT: HIGH 12V: OK LOW: Fault
adc comm
TSAL = HIGH safe, LOW unsafe (IMD_COCKPIT = HIGH safe, LOW fault BMS_COCKPIT = HIGH safe, LOW fault)
cells com
HANDCART is PULL-DOWN TSAL is PULL-DOWN IMD_COCKPIT is PULL-DOWN AMS_LED is PULL-DOWN 5V_PROG is PULL-DOWN
VOLTAGE REGULATION
RAIL PRESENCE LEDs

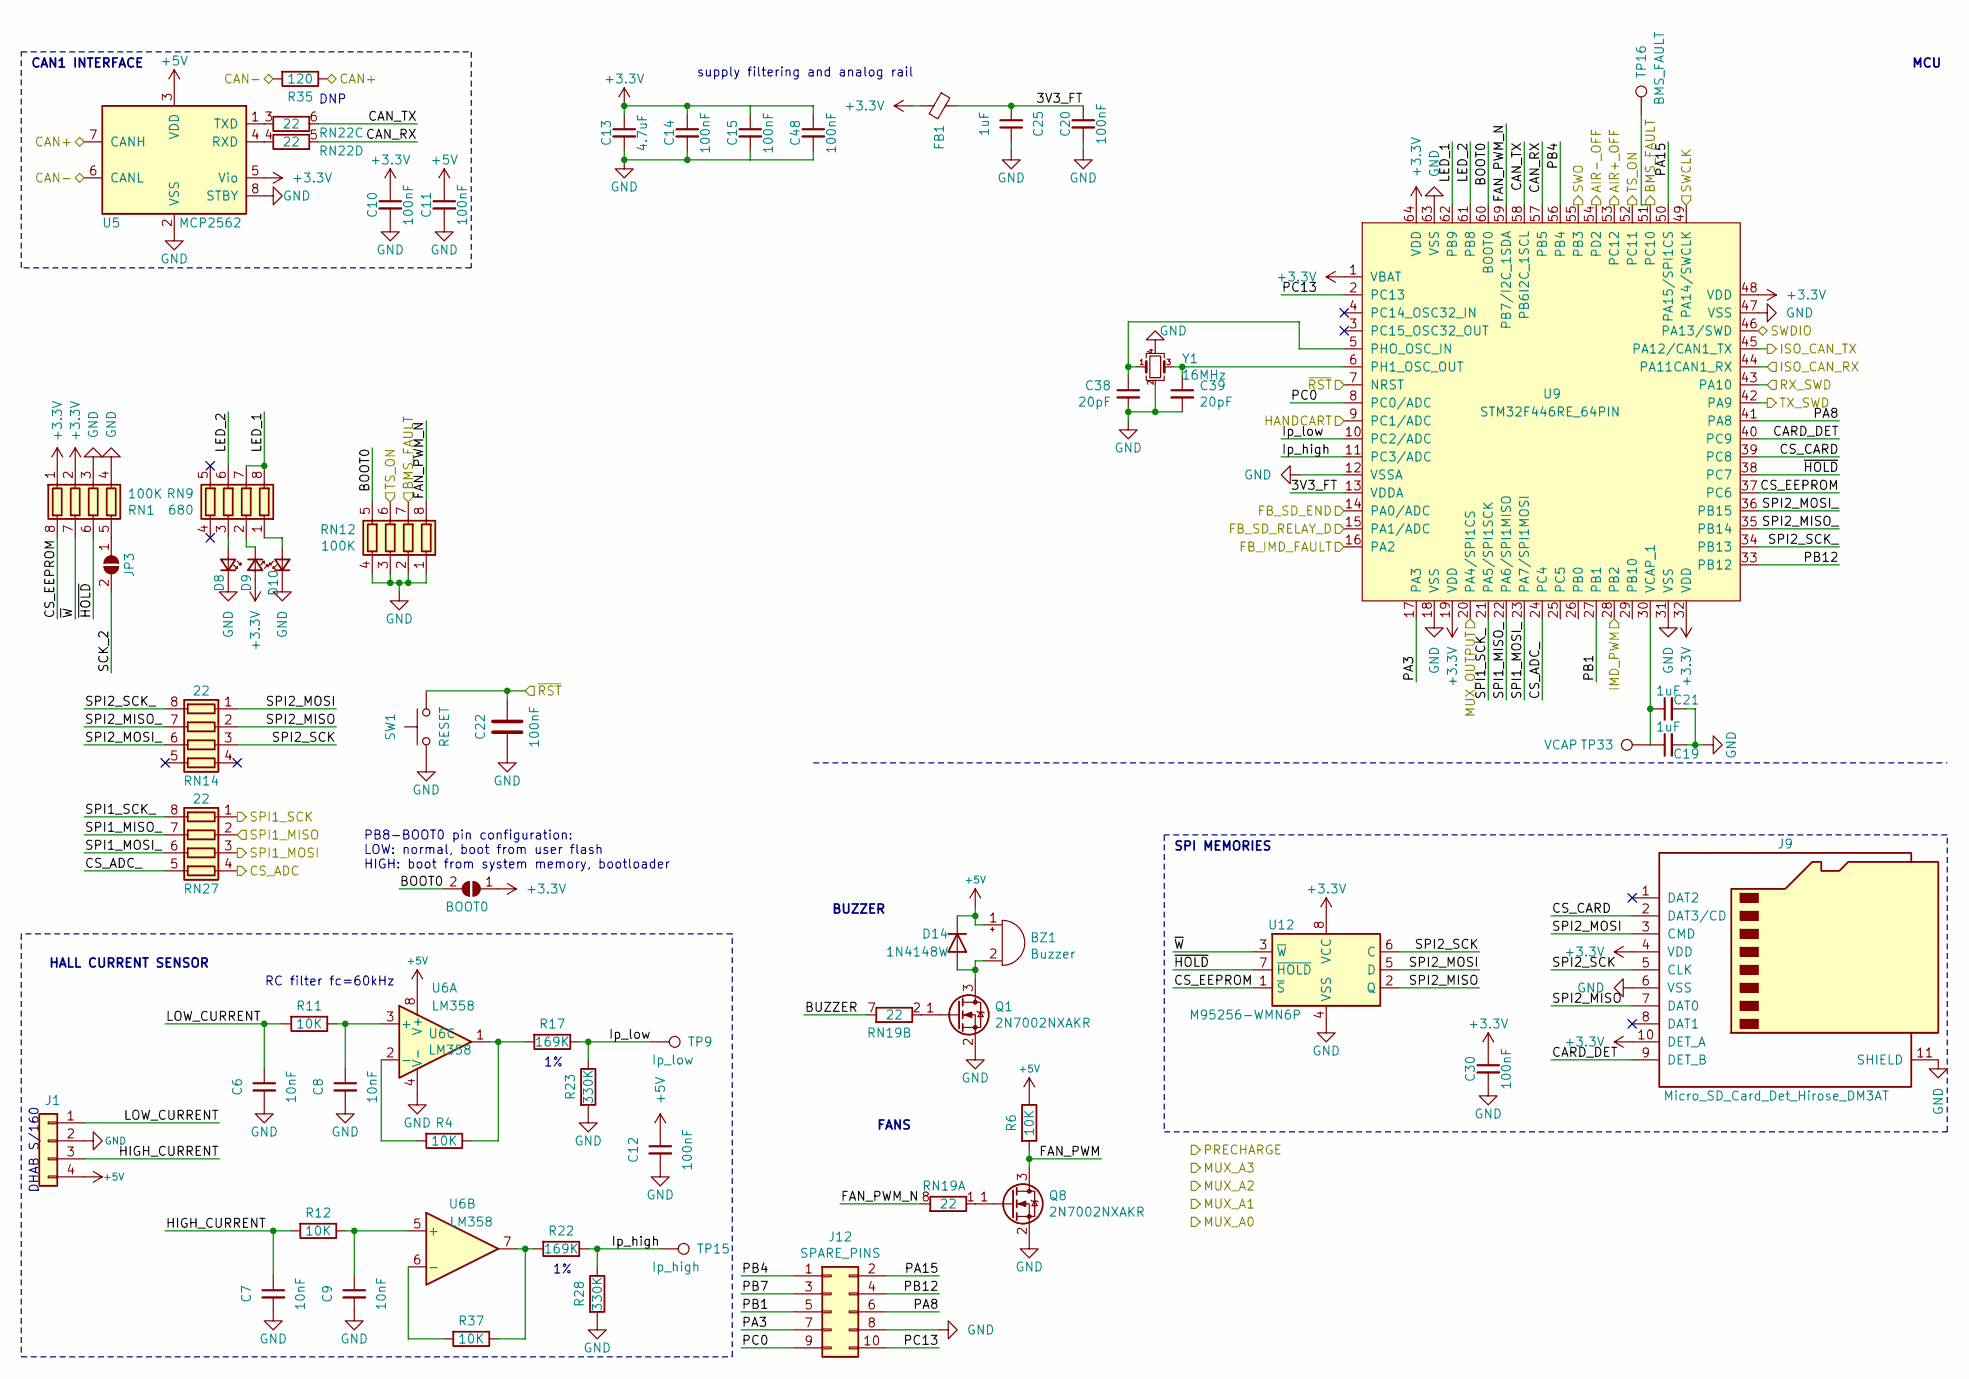
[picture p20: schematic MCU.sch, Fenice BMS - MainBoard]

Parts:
BZ1: Buzzer; Buzzer_TDK_SD1614TT_D16mm_H14mm_P5mm
C6, C7, C8, C9: 10nF; C_0603_1608Metric
C10, C11, C12, C14, C15, C20, C22, C30, C48: 100nF; C_0603_1608Metric
C13: 4.7uF; C_0805_2012Metric
C19, C21, C25: 1uF; C_0805_2012Metric
C38, C39: 20pF; C_0603_1608Metric
D8: LED_Small; LED_reverse_mount_cilindrical
D9, D10: LED_Small; LED_0603_1608Metric_Castellated
D14: 1N4148W; D_SOD-123
FB1: FerriteBead_Small; L_0603_1608Metric_Pad1.05x0.95mm_HandSolder
J1: CONN_1x4; Molex_Micro-Fit_3.0_43650-0415_1x04_P3.00mm_Vertical
J9: Micro_SD_Card_Det_Hirose_DM3AT; microSD_HC_Hirose_DM3AT-SF-PEJM5
J12: SPARE_PINS; PinHeader_2x05_P2.54mm_Vertical
JP1: BOOT0; SolderJumper-2_P1.3mm_Open_RoundedPad1.0x1.5mm
JP3: SolderJumper_2_Open; SolderJumper-2_P1.3mm_Open_RoundedPad1.0x1.5mm
Q1, Q8: 2N7002NXAKR; SOT-23
R4, R6, R11, R12, R37: 10K; R_0603_1608Metric
R17, R22: 169K; R_0603_1608Metric
R23, R28: 330K; R_0603_1608Metric
R35: 120; R_0805_2012Metric
RN1, RN12: 100K; R_Array_Convex_4x0603
RN9: 680; R_Array_Convex_4x0603
RN14, RN19, RN22, RN27: 22; R_Array_Convex_4x0603
SW1: RESET; SW_SPST_FSMSM
TP9: Ip_low; TestPoint_Pad_D1.0mm
TP15: Ip_high; TestPoint_Pad_D1.0mm
TP16: BMS_FAULT; TestPoint_Pad_D1.0mm
TP33: VCAP; TestPoint_Pad_D1.0mm
U5: MCP2562; SOIC-8_3.9x4.9mm_P1.27mm
U6: LM358; TSOT-23-8
U9: STM32F446RE_64PIN; LQFP-64_10x10mm_P0.5mm
U12: M95256-WMN6P; TSSOP-8_4.4x3mm_P0.65mm
Y1: 16MHz; Crystal_SMD_3225-4Pin_3.2x2.5mm

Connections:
+5V: BZ1.1 (-), C11.1, C12.1, D14.1 (K), J1.4, R6.1, U5.3 (VDD), U6.8 (V+); also elsewhere on the board
/AIRs/AIR+_OFF: U9.53 (PC12); also elsewhere on the board
/AIRs/AIR-_OFF: U9.54 (PD2); also elsewhere on the board
/CAN+: R35.1, U5.7 (CANH); also elsewhere on the board
/CAN-: R35.2, U5.6 (CANL); also elsewhere on the board
/HANDCART: U9.9 (PC1/ADC)
/HV/ADC_MISO: RN27.2 (R2.1); also elsewhere on the board
/HV/ADC_MOSI: RN27.3 (R3.1); also elsewhere on the board
/HV/ADC_SCLK: RN27.1 (R1.1); also elsewhere on the board
/HV/ADC_~CS~: RN27.4 (R4.1); also elsewhere on the board
/IMD_PWM: U9.28 (PB2); also elsewhere on the board
/MCU/3V3_FT: C20.1, C25.2, FB1.1, U9.13 (VDDA)
/MCU/BMS_FAULT: RN12.7 (R2.2), TP16.1, U9.51 (PC10); also elsewhere on the board
/MCU/BOOT0: JP1.2 (B), RN12.5 (R4.2), U9.60 (BOOT0)
/MCU/BUZZER: RN19.7 (R2.2)
/MCU/CAN_RX: RN22.5 (R4.2), U9.57 (PB5)
/MCU/CAN_TX: RN22.6 (R3.2), U9.58 (PB6I2C_1SCL)
/MCU/CARD_DET: J9.9 (DET_B), U9.40 (PC9)
/MCU/CS_ADC_: RN27.5 (R4.2), U9.24 (PC4)
/MCU/CS_CARD: J9.2 (DAT3/CD), U9.39 (PC8)
/MCU/CS_EEPROM: RN1.8 (R1.2), U9.37 (PC6), U12.1 (~S)
/MCU/FAN_PWM: Q8.3 (D), R6.2
/MCU/FAN_PWM_N: RN12.8 (R1.2), RN19.8 (R1.2), U9.59 (PB7/I2C_1SDA)
/MCU/FB_IMD_FAULT: U9.16 (PA2)
/MCU/FB_SD_END: U9.14 (PA0/ADC); also elsewhere on the board
/MCU/FB_SD_RELAY_D: U9.15 (PA1/ADC)
/MCU/HIGH_CURRENT: C7.1, J1.3, R12.2
/MCU/ISO_CAN_RX: U9.44 (PA11CAN1_RX); also elsewhere on the board
/MCU/ISO_CAN_TX: U9.45 (PA12/CAN1_TX); also elsewhere on the board
/MCU/Ip_high: R22.1, R28.1, TP15.1, U9.11 (PC3/ADC)
/MCU/Ip_low: R17.1, R23.1, TP9.1, U9.10 (PC2/ADC)
/MCU/LED_1: RN9.7 (R2.2), RN9.8 (R1.2), U9.62 (PB9)
/MCU/LED_2: RN9.6 (R3.2), U9.61 (PB8)
/MCU/LOW_CURRENT: C6.1, J1.1, R11.2
/MCU/MUX_OUTPUT: U9.20 (PA4/SPI1CS); also elsewhere on the board
/MCU/PA3: J12.7, U9.17 (PA3)
/MCU/PA8: J12.6, U9.41 (PA8)
/MCU/PA15: J12.2, U9.50 (PA15/SPI1CS)
/MCU/PB1: J12.5, U9.27 (PB1)
/MCU/PB4: J12.1, U9.56 (PB4)
/MCU/PB7: J12.3
/MCU/PB12: J12.4, U9.33 (PB12)
/MCU/PC0: J12.9, U9.8 (PC0/ADC)
/MCU/PC13: J12.10, U9.2 (PC13)
/MCU/SCK_2: JP3.2 (B)
/MCU/SPI1_MISO_: RN27.7 (R2.2), U9.22 (PA6/SPI1MISO)
/MCU/SPI1_MOSI_: RN27.6 (R3.2), U9.23 (PA7/SPI1MOSI)
/MCU/SPI1_SCK_: RN27.8 (R1.2), U9.21 (PA5/SPI1SCK)
/MCU/SPI2_MISO: J9.7 (DAT0), RN14.2 (R2.1), U12.2 (Q)
/MCU/SPI2_MISO_: RN14.7 (R2.2), U9.35 (PB14)
/MCU/SPI2_MOSI: J9.3 (CMD), RN14.1 (R1.1), U12.5 (D)
/MCU/SPI2_MOSI_: RN14.6 (R3.2), U9.36 (PB15)
/MCU/SPI2_SCK: J9.5 (CLK), RN14.3 (R3.1), U12.6 (C)
/MCU/SPI2_SCK_: RN14.8 (R1.2), U9.34 (PB13)
/MCU/TS_ON: RN12.6 (R3.2), U9.52 (PC11); also elsewhere on the board
/MCU/~HOLD~: RN1.6 (R3.2), U9.38 (PC7), U12.7 (~HOLD)
/MCU/~W~: RN1.7 (R2.2), U12.3 (~W)
/NRST_MCU: C22.1, SW1.1, U9.7 (NRST); also elsewhere on the board
/RX_MCU: U9.43 (PA10); also elsewhere on the board
/SWCLK_MCU: U9.49 (PA14/SWCLK); also elsewhere on the board
/SWDIO_MCU: U9.46 (PA13/SWD); also elsewhere on the board
/SWO_MCU: U9.55 (PB3); also elsewhere on the board
/TX_MCU: U9.42 (PA9); also elsewhere on the board
GND: C6.2, C7.2, C8.2, C9.2, C10.2, C11.2, C12.2, C13.2, C14.2, C15.2, C19.2, C20.2, C21.2, C22.2, C25.1, C30.2, C38.2, C39.2, C48.2, D8.1 (K), D10.1 (K), J1.2, J9.6 (VSS), J9.11 (SHIELD), J12.8, Q1.2 (S), Q8.2 (S), R23.2, R28.2, RN1.3 (R3.1), RN1.4 (R4.1), RN12.1 (R1.1), RN12.2 (R2.1), RN12.3 (R3.1), RN12.4 (R4.1), SW1.2, U5.2 (VSS), U5.8 (STBY), U6.4 (V-), U9.12 (VSSA), U9.18 (VSS), U9.31 (VSS), U9.47 (VSS), U9.63 (VSS), U12.4 (VSS), Y1.2, Y1.4; also elsewhere on the board
unnamed: BZ1.2 (+), D14.2 (A), Q1.3 (D)
unnamed: C8.1, R11.1, U6.3 (+)
unnamed: C9.1, R12.1, U6.5 (+)
unnamed: C19.1, C21.1, TP33.1, U9.30 (VCAP_1)
unnamed: C38.1, U9.5 (PHO_OSC_IN), Y1.1
unnamed: C39.1, U9.6 (PH1_OSC_OUT), Y1.3
unnamed: D8.2 (A), RN9.3 (R3.1)
unnamed: D9.1 (K), RN9.2 (R2.1)
unnamed: D10.2 (A), RN9.1 (R1.1)
unnamed: JP3.1 (A), RN1.5 (R4.2)
unnamed: Q1.1 (G), RN19.2 (R2.1)
unnamed: Q8.1 (G), RN19.1 (R1.1)
unnamed: R4.2, U6.2 (-)
unnamed: R4.1, R17.2, U6.1
unnamed: R22.2, R37.1, U6.7
unnamed: R37.2, U6.6 (-)
unnamed: RN22.3 (R3.1), U5.1 (TXD)
unnamed: RN22.4 (R4.1), U5.4 (RXD)

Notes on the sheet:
CAN1 INTERFACE
HALL CURRENT SENSOR
MCU
supply filtering and analog rail
SPI MEMORIES
PB8-BOOT0 pin configuration: LOW: normal, boot from user flash HIGH: boot from system memory, bootloader
DHAB S/160
RC filter fc=60kHz
DNP
FANS
BUZZER

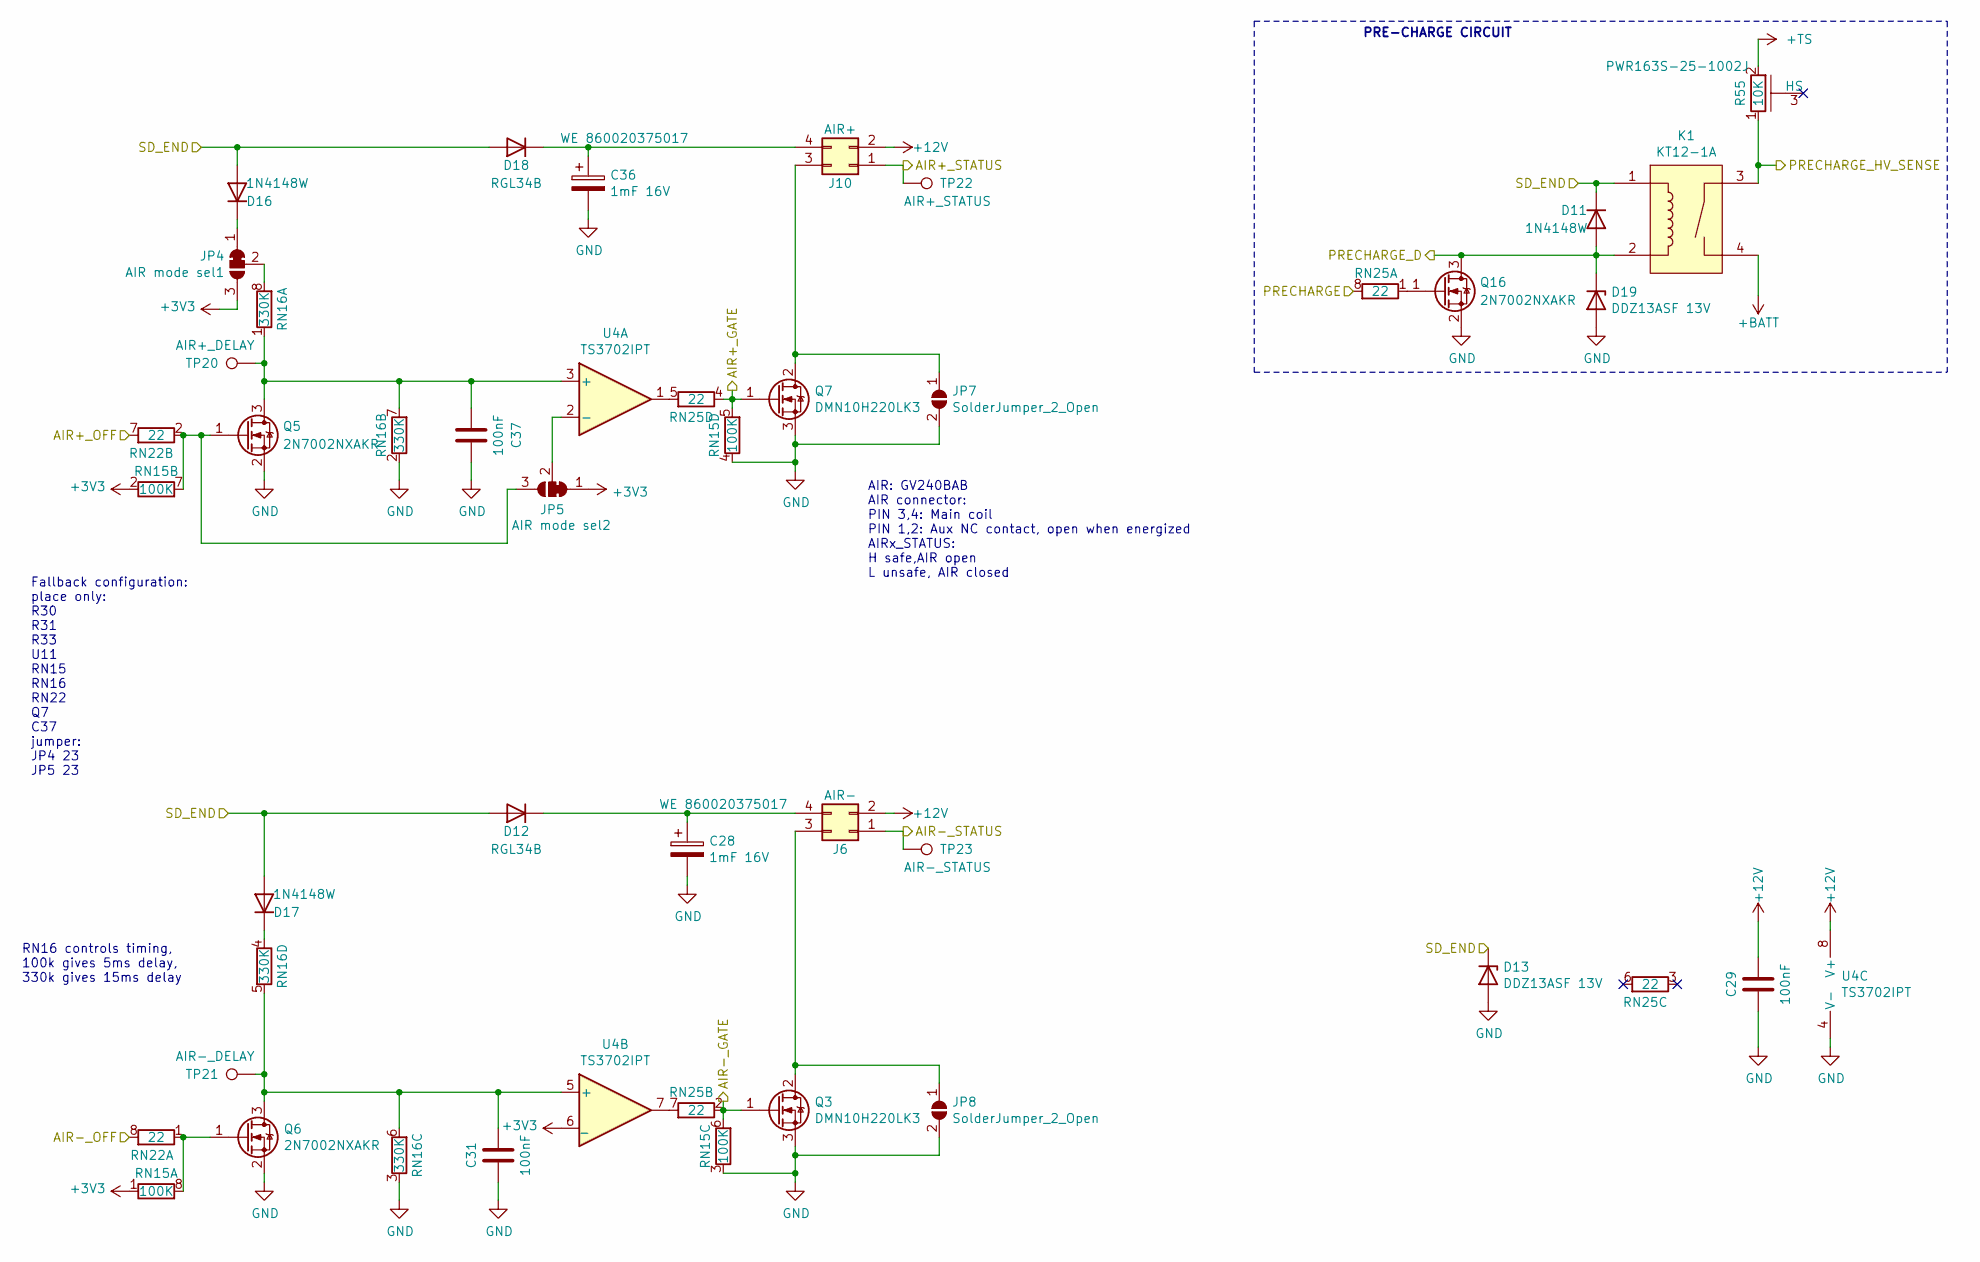
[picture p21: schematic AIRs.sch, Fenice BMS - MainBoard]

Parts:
C28, C36: 1mF 16V; CP_Radial_D10.0mm_P5.00mm; Partname WE 860020375017
C29, C31, C37: 100nF; C_0603_1608Metric
D11, D16, D17: 1N4148W; D_SOD-123
D12, D18: RGL34B; D_MiniMELF
D13, D19: DDZ13ASF 13V; D_SOD-323
J6: AIR-; Molex_Micro-Fit_3.0_43045-0412_2x02_P3.00mm_Vertical
J10: AIR+; Molex_Micro-Fit_3.0_43045-0412_2x02_P3.00mm_Vertical
JP4: AIR mode sel1; SolderJumper-3_P1.3mm_Bridged12_RoundedPad1.0x1.5mm
JP5: AIR mode sel2; SolderJumper-3_P1.3mm_Bridged12_RoundedPad1.0x1.5mm
JP7, JP8: SolderJumper_2_Open; SolderJumper-2_P1.3mm_Open_RoundedPad1.0x1.5mm
K1: KT12-1A; KT12_THT
Q3, Q7: DMN10H220LK3; TO-252-2
Q5, Q6, Q16: 2N7002NXAKR; SOT-23
R55: 10K; PWR163; Partname PWR163S-25-1002J
RN15: 100K; R_Array_Convex_4x0603
RN16: 330K; R_Array_Convex_4x0603
RN22, RN25: 22; R_Array_Convex_4x0603
TP20: AIR+_DELAY; TestPoint_Pad_D1.0mm
TP21: AIR-_DELAY; TestPoint_Pad_D1.0mm
TP22: AIR+_STATUS; TestPoint_Pad_D1.0mm
TP23: AIR-_STATUS; TestPoint_Pad_D1.0mm
U4: TS3702IPT; TSSOP-8_4.4x3mm_P0.65mm

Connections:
+12V: C29.1, J6.2, J10.2, U4.8 (V+); also elsewhere on the board
+BATT: K1.4; also elsewhere on the board
+TS: R55.2; also elsewhere on the board
/AIRs/AIR+_GATE: Q7.1 (G), RN15.5 (R4.2), RN25.4 (R4.1); also elsewhere on the board
/AIRs/AIR+_OFF: RN22.7 (R2.2); also elsewhere on the board
/AIRs/AIR+_STATUS: J10.1, TP22.1; also elsewhere on the board
/AIRs/AIR-_GATE: Q3.1 (G), RN15.6 (R3.2), RN25.2 (R2.1); also elsewhere on the board
/AIRs/AIR-_OFF: RN22.8 (R1.2); also elsewhere on the board
/AIRs/AIR-_STATUS: J6.1, TP23.1; also elsewhere on the board
/AIRs/PRECHARGE: RN25.8 (R1.2)
/AIRs/PRECHARGE_D: D11.2 (A), D19.1 (K), K1.2, Q16.3 (D); also elsewhere on the board
/AIRs/PRECHARGE_HV_SENSE: K1.3, R55.1; also elsewhere on the board
/SD_END: D11.1 (K), D12.2 (A), D13.1 (K), D16.2 (A), D17.2 (A), D18.2 (A), K1.1; also elsewhere on the board
GND: C28.2, C29.2, C31.2, C36.2, C37.2, D13.2 (A), D19.2 (A), JP7.2 (B), JP8.2 (B), Q3.3 (S), Q5.2 (S), Q6.2 (S), Q7.3 (S), Q16.2 (S), RN15.3 (R3.1), RN15.4 (R4.1), RN16.2 (R2.1), RN16.3 (R3.1), U4.4 (V-); also elsewhere on the board
unnamed: C28.1, D12.1 (K), J6.4
unnamed: C31.1, Q6.3 (D), RN16.5 (R4.2), RN16.6 (R3.2), TP21.1, U4.5 (+)
unnamed: C36.1, D18.1 (K), J10.4
unnamed: C37.1, Q5.3 (D), RN16.1 (R1.1), RN16.7 (R2.2), TP20.1, U4.3 (+)
unnamed: D16.1 (K), JP4.1 (A)
unnamed: D17.1 (K), RN16.4 (R4.1)
unnamed: J6.3, JP8.1 (A), Q3.2 (D)
unnamed: J10.3, JP7.1 (A), Q7.2 (D)
unnamed: JP4.2 (C), RN16.8 (R1.2)
unnamed: JP5.2 (C), U4.2 (-)
unnamed: JP5.3 (B), Q5.1 (G), RN15.7 (R2.2), RN22.2 (R2.1)
unnamed: Q6.1 (G), RN15.8 (R1.2), RN22.1 (R1.1)
unnamed: Q16.1 (G), RN25.1 (R1.1)
unnamed: RN25.5 (R4.2), U4.1
unnamed: RN25.7 (R2.2), U4.7

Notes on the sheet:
AIR: GV240BAB AIR connector: PIN 3,4: Main coil PIN 1,2: Aux NC contact, open when energized AIRx_STATUS: H safe,AIR open L unsafe, AIR closed
PRE-CHARGE CIRCUIT
RN16 controls timing, 100k gives 5ms delay, 330k gives 15ms delay
Fallback configuration: place only: R30 R31 R33 U11 RN15 RN16 RN22 Q7 C37 jumper: JP4 23 JP5 23

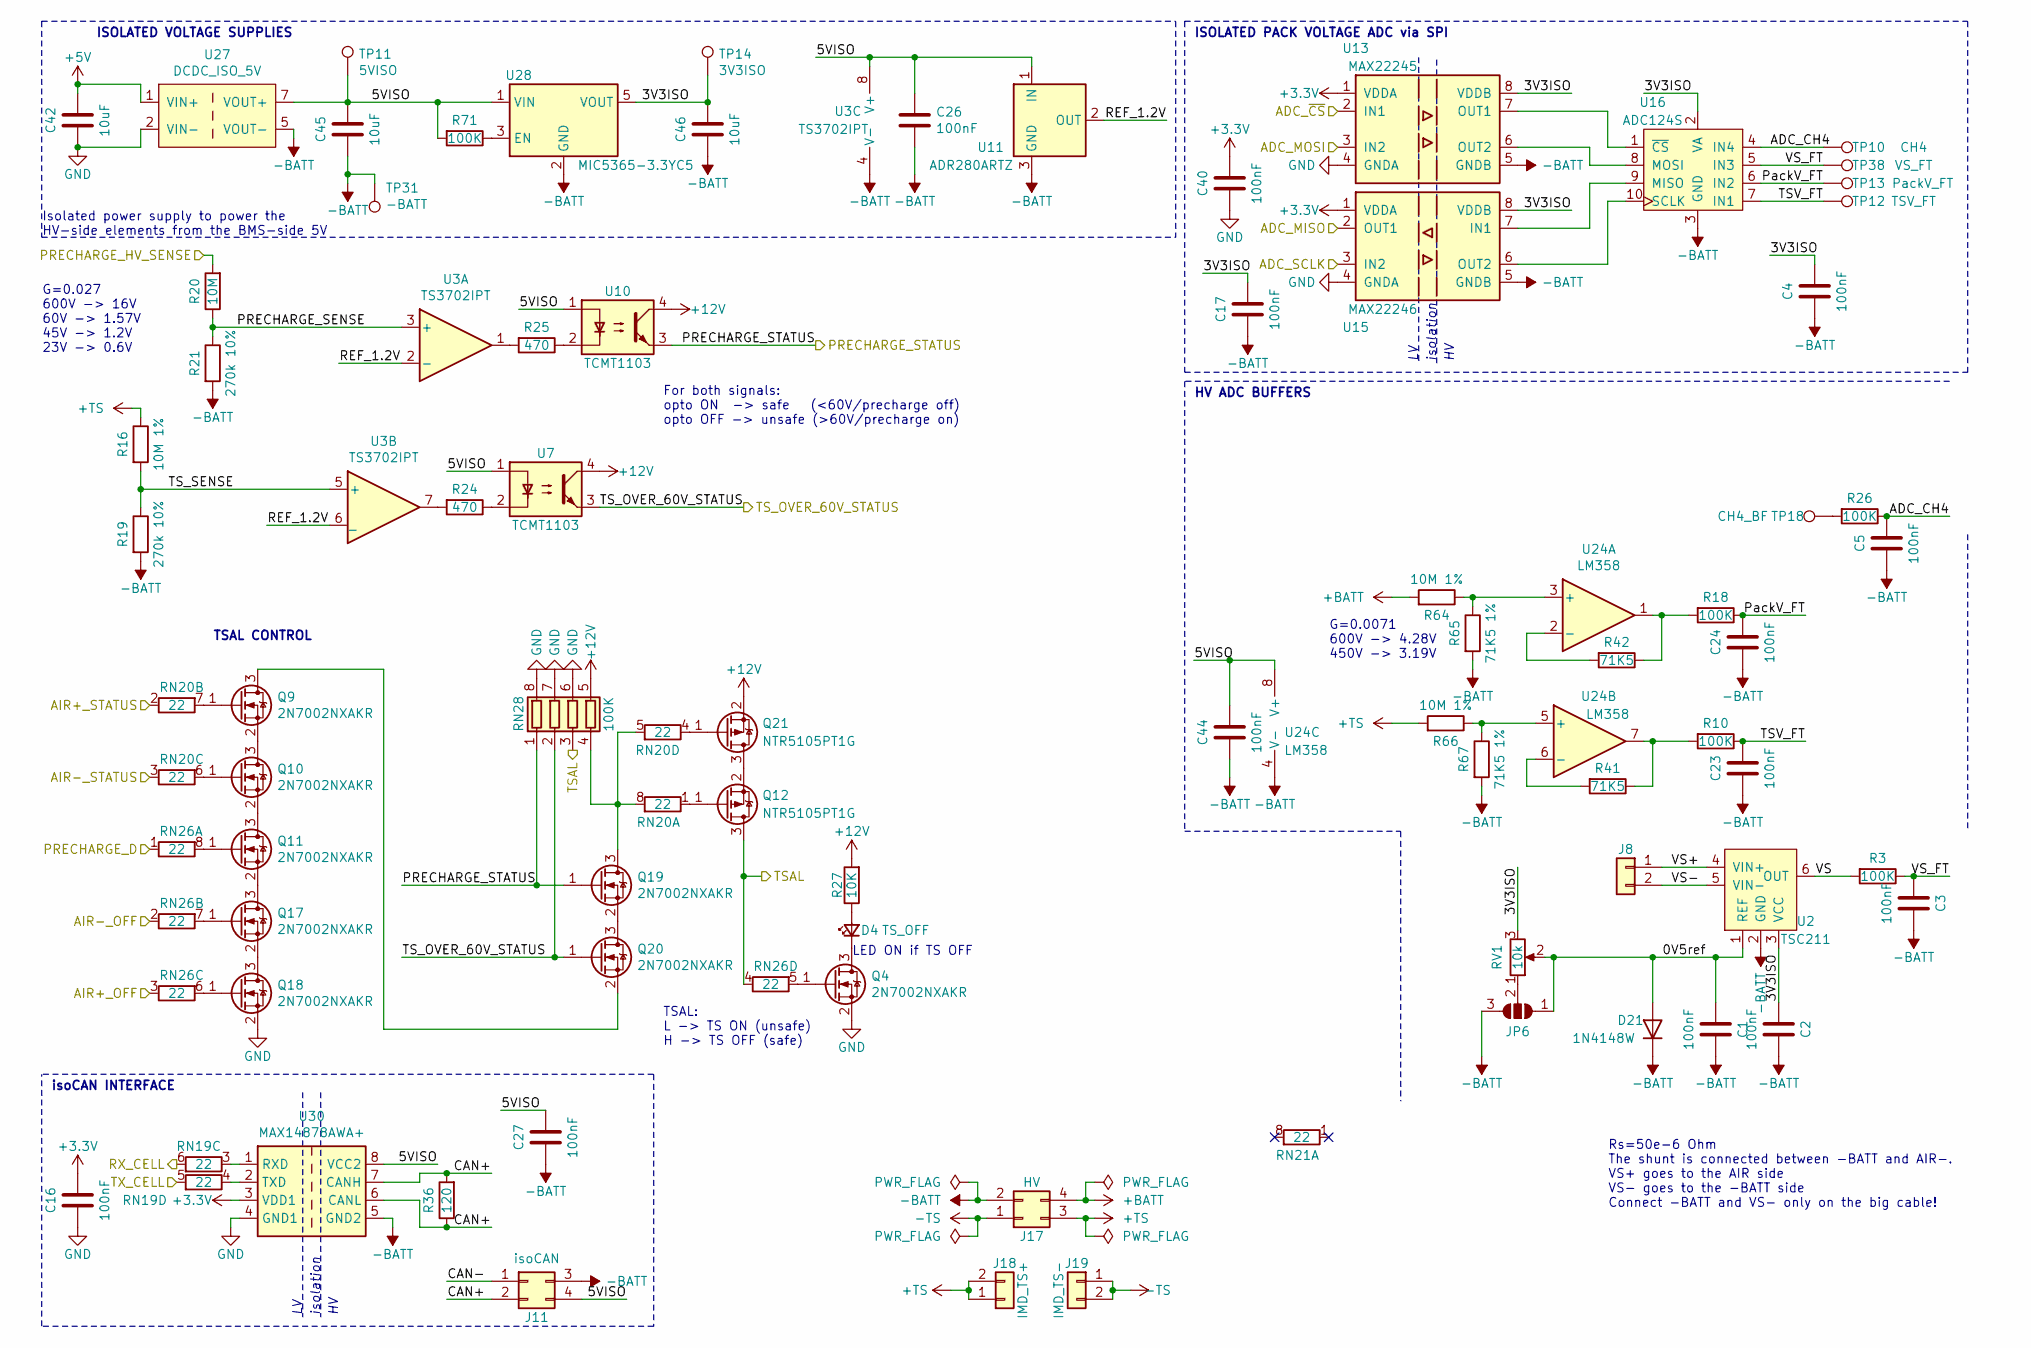
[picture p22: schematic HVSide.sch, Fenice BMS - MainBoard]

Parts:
C1, C2, C3, C4, C5, C16, C17, C23, C24, C26, C27, C40, C44: 100nF; C_0603_1608Metric
C42, C45, C46: 10uF; C_0805_2012Metric
D4: TS_OFF; LED_0603_1608Metric_Castellated
D21: 1N4148W; D_SOD-123
J8: CONN_1X2; Molex_Micro-Fit_3.0_43650-0215_1x02_P3.00mm_Vertical
J11: isoCAN; Molex_Micro-Fit_3.0_43045-0412_2x02_P3.00mm_Vertical
J17: HV; Molex_Mega-Fit_76829-0104_2x02_P5.70mm_Vertical
J18: IMD_TS+; Molex_Micro-Fit_3.0_43650-0215_1x02_P3.00mm_Vertical
J19: IMD_TS-; Molex_Micro-Fit_3.0_43650-0215_1x02_P3.00mm_Vertical
JP6: SolderJumper_3_Open; SolderJumper-3_P1.3mm_Open_RoundedPad1.0x1.5mm
Q4, Q9, Q10, Q11, Q17, Q18, Q19, Q20: 2N7002NXAKR; SOT-23
Q12, Q21: NTR5105PT1G; SOT-23
R3, R10, R18, R26, R71: 100K; R_0603_1608Metric
R16, R64, R66: 10M 1%; R_2010_5025Metric
R19, R21: 270k 10%; R_0603_1608Metric
R20: 10M; R_2010_5025Metric
R24, R25: 470; R_0603_1608Metric
R27: 10K; R_0603_1608Metric
R36: 120; R_0805_2012Metric
R41, R42: 71K5; R_0603_1608Metric
R65, R67: 71K5 1%; R_0603_1608Metric
RN19, RN20, RN21, RN26: 22; R_Array_Convex_4x0603
RN28: 100K; R_Array_Convex_4x0603
RV1: 10k; Potentiometer_Bourns_3314J_Vertical
TP10: CH4; TestPoint_Pad_D1.0mm
TP11: 5VISO; TestPoint_Pad_D1.0mm
TP12: TSV_FT; TestPoint_Pad_D1.0mm
TP13: PackV_FT; TestPoint_Pad_D1.0mm
TP14: 3V3ISO; TestPoint_Pad_D1.0mm
TP18: CH4_BF; TestPoint_Pad_D1.0mm
TP31: -BATT; TestPoint_GNDedge
TP38: VS_FT; TestPoint_Pad_D1.0mm
U2: TSC211; SOT-363_SC-70-6
U3: TS3702IPT; TSSOP-8_4.4x3mm_P0.65mm
U7, U10: TCMT1103; SOP-4_4.4x2.6mm_P1.27mm
U11: ADR280ARTZ; SOT-23
U13: MAX22245; SOIC-8_7.5x5.85mm_P1.27mm
U15: MAX22246; SOIC-8_7.5x5.85mm_P1.27mm
U16: ADC124S; VSSOP-10_3x3mm_P0.5mm
U24: LM358; TSOT-23-8
U27: DCDC_ISO_5V; RFMM_0505S
U28: MIC5365-3.3YC5; SOT-353_SC-70-5
U30: MAX14878AWA+; SOIC-8W_5.3x5.3mm_P1.27mm

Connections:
+5V: C42.1, U27.1 (VIN+); also elsewhere on the board
+12V: Q21.2 (S), R27.2, RN28.5 (R4.2), U7.4, U10.4; also elsewhere on the board
+BATT: J17.4, R64.2; also elsewhere on the board
+TS: J17.3, J18.1, J18.2, R16.1, R66.2; also elsewhere on the board
-BATT: C1.2, C2.1, C3.1, C4.2, C5.2, C17.2, C23.2, C24.2, C26.2, C27.2, C44.2, C45.2, C46.2, D21.1 (K), J11.3, J17.2, JP6.3 (B), R19.2, R21.2, R65.2, R67.2, TP31.1, U2.2 (GND), U3.4 (V-), U11.3 (GND), U13.5 (GNDB), U15.5 (GNDB), U16.3 (GND), U24.4 (V-), U27.5 (VOUT-), U28.2 (GND), U30.5 (GND2)
-TS: J17.1, J19.1, J19.2
/AIRs/AIR+_OFF: RN26.3 (R3.1); also elsewhere on the board
/AIRs/AIR+_STATUS: RN20.2 (R2.1); also elsewhere on the board
/AIRs/AIR-_OFF: RN26.2 (R2.1); also elsewhere on the board
/AIRs/AIR-_STATUS: RN20.3 (R3.1); also elsewhere on the board
/AIRs/PRECHARGE_D: RN26.1 (R1.1); also elsewhere on the board
/AIRs/PRECHARGE_HV_SENSE: R20.2; also elsewhere on the board
/HV/0V5ref: C1.1, D21.2 (A), JP6.1 (A), RV1.2, U2.1 (REF)
/HV/3V3ISO: C2.2, C4.1, C17.1, C46.1, RV1.3, TP14.1, U2.3 (VCC), U13.8 (VDDB), U15.8 (VDDB), U16.2 (VA), U28.5 (VOUT)
/HV/5VISO: C26.1, C27.1, C44.1, C45.1, J11.4, R71.2, TP11.1, U3.8 (V+), U7.1, U10.1, U11.1 (IN), U24.8 (V+), U27.7 (VOUT+), U28.1 (VIN), U30.8 (VCC2)
/HV/ADC_CH4: C5.1, R26.1, TP10.1, U16.4 (IN4)
/HV/ADC_MISO: U15.2 (OUT1); also elsewhere on the board
/HV/ADC_MOSI: U13.3 (IN2); also elsewhere on the board
/HV/ADC_SCLK: U15.3 (IN2); also elsewhere on the board
/HV/ADC_~CS~: U13.2 (IN1); also elsewhere on the board
/HV/CAN+: J11.2, R36.1, R36.2, U30.6 (CANL), U30.7 (CANH)
/HV/CAN-: J11.1
/HV/PRECHARGE_SENSE: R20.1, R21.1, U3.3 (+)
/HV/PRECHARGE_STATUS: Q19.1 (G), RN28.1 (R1.1), U10.3; also elsewhere on the board
/HV/PackV_FT: C24.1, R18.1, TP13.1, U16.6 (IN2)
/HV/REF_1.2V: U3.2 (-), U3.6 (_), U11.2 (OUT)
/HV/TSV_FT: C23.1, R10.1, TP12.1, U16.7 (IN1)
/HV/TS_OVER_60V_STATUS: Q20.1 (G), RN28.2 (R2.1), U7.3; also elsewhere on the board
/HV/TS_SENSE: R16.2, R19.1, U3.5 (+)
/HV/VS: R3.2, U2.6 (OUT)
/HV/VS+: J8.1, U2.4 (VIN+)
/HV/VS-: J8.2, U2.5 (VIN-)
/HV/VS_FT: C3.2, R3.1, TP38.1, U16.5 (IN3)
/MCU/ISO_CAN_RX: RN19.6 (R3.2); also elsewhere on the board
/MCU/ISO_CAN_TX: RN19.5 (R4.2); also elsewhere on the board
/TSAL: Q12.3 (D), RN26.4 (R4.1), RN28.3 (R3.1); also elsewhere on the board
GND: C16.2, C40.2, C42.2, Q4.2 (S), Q18.2 (S), RN28.6 (R3.2), RN28.7 (R2.2), RN28.8 (R1.2), U13.4 (GNDA), U15.4 (GNDA), U27.2 (VIN-), U30.4 (GND1); also elsewhere on the board
unnamed: D4.1 (K), Q4.3 (D)
unnamed: D4.2 (A), R27.1
unnamed: JP6.2 (C), RV1.1
unnamed: Q4.1 (G), RN26.5 (R4.2)
unnamed: Q9.1 (G), RN20.7 (R2.2)
unnamed: Q10.1 (G), RN20.6 (R3.2)
unnamed: Q10.2 (S), Q11.3 (D)
unnamed: Q9.2 (S), Q10.3 (D)
unnamed: Q11.1 (G), RN26.8 (R1.2)
unnamed: Q11.2 (S), Q17.3 (D)
unnamed: Q12.1 (G), RN20.1 (R1.1)
unnamed: Q12.2 (S), Q21.3 (D)
unnamed: Q17.1 (G), RN26.7 (R2.2)
unnamed: Q17.2 (S), Q18.3 (D)
unnamed: Q18.1 (G), RN26.6 (R3.2)
unnamed: Q19.2 (S), Q20.3 (D)
unnamed: Q19.3 (D), RN20.5 (R4.2), RN20.8 (R1.2), RN28.4 (R4.1)
unnamed: Q9.3 (D), Q20.2 (S)
unnamed: Q21.1 (G), RN20.4 (R4.1)
unnamed: R10.2, R41.1, U24.7
unnamed: R18.2, R42.1, U24.1
unnamed: R24.1, U7.2
unnamed: R24.2, U3.7
unnamed: R25.1, U10.2
unnamed: R25.2, U3.1
unnamed: R26.2, TP18.1
unnamed: R41.2, U24.6 (-)
unnamed: R42.2, U24.2 (-)
unnamed: R64.1, R65.1, U24.3 (+)
unnamed: R66.1, R67.1, U24.5 (+)
unnamed: R71.1, U28.3 (EN)
unnamed: RN19.3 (R3.1), U30.1 (RXD)
unnamed: RN19.4 (R4.1), U30.2 (TXD)
unnamed: U13.6 (OUT2), U16.8 (MOSI)
unnamed: U13.7 (OUT1), U16.1 (~CS~)
unnamed: U15.6 (OUT2), U16.10 (SCLK)
unnamed: U15.7 (IN1), U16.9 (MISO)

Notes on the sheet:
ISOLATED VOLTAGE SUPPLIES
HV ADC BUFFERS
isoCAN INTERFACE
isolation
Isolated power supply to power the HV-side elements from the BMS-side 5V
Rs=50e-6 Ohm The shunt is connected between -BATT and AIR-. VS+ goes to the AIR side VS- goes to the -BATT side Connect -BATT and VS- only on the big cable!
G=0.0071 600V -> 4.28V 450V -> 3.19V
ISOLATED PACK VOLTAGE ADC via SPI
TSAL CONTROL
LED ON if TS OFF
TSAL: L -> TS ON (unsafe) H -> TS OFF (safe)
G=0.027 600V -> 16V 60V -> 1.57V 45V -> 1.2V 23V -> 0.6V
For both signals: opto ON -> safe (<60V/precharge off) opto OFF -> unsafe (>60V/precharge on)

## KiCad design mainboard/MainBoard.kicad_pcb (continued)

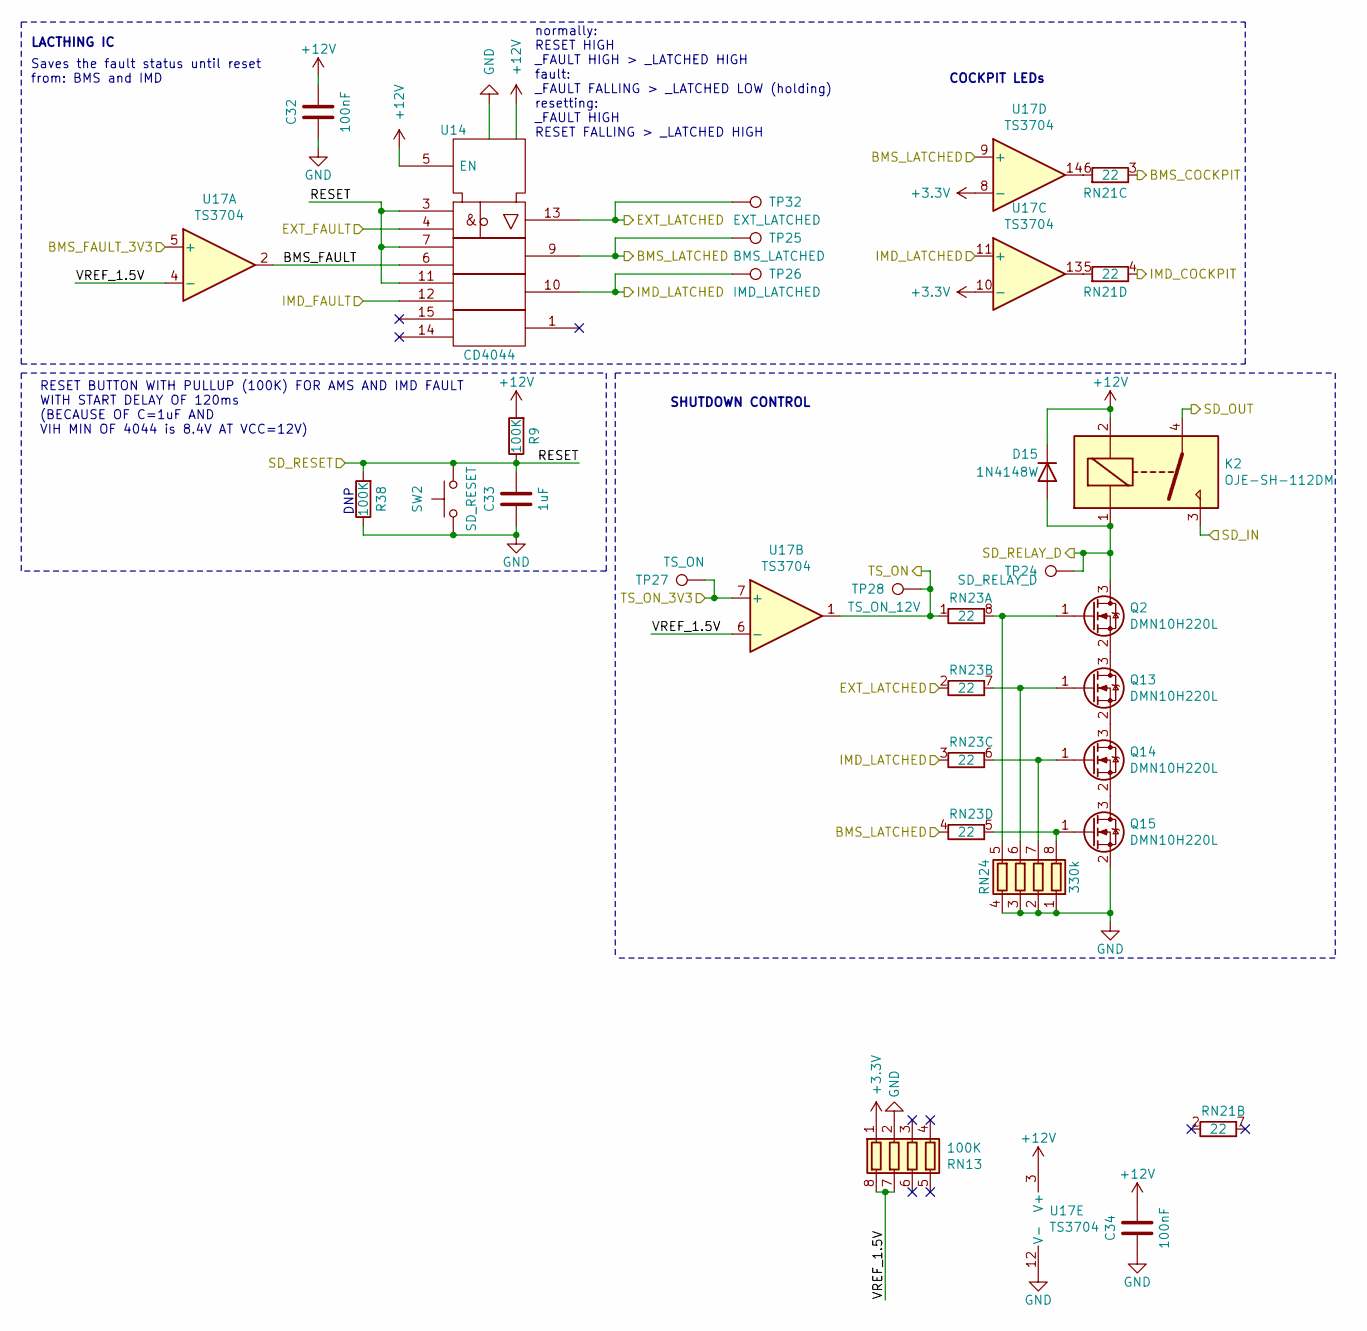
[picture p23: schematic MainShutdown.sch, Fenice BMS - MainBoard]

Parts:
C32, C34: 100nF; C_0603_1608Metric
C33: 1uF; C_0805_2012Metric
D15: 1N4148W; D_SOD-123
K2: OJE-SH-112DM
Q2, Q13, Q14, Q15: DMN10H220L; SOT-23
R9, R38: 100K; R_0603_1608Metric
RN13: 100K; R_Array_Convex_4x0603
RN21, RN23: 22; R_Array_Convex_4x0603
RN24: 330k; R_Array_Convex_4x0603
SW2: SD_RESET; SW_SPST_FSMSM
TP24: SD_RELAY_D; TestPoint_Pad_D1.0mm
TP25: BMS_LATCHED; TestPoint_Pad_D1.0mm
TP26: IMD_LATCHED; TestPoint_Pad_D1.0mm
TP27: TS_ON; TestPoint_Pad_D1.0mm
TP28: TS_ON_12V; TestPoint_Pad_D1.0mm
TP32: EXT_LATCHED; TestPoint_Pad_D1.0mm
U14: CD4044; TSSOP-16_4.4x5mm_P0.65mm
U17: TS3704; TSSOP-14_4.4x5mm_P0.65mm

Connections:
+12V: C32.1, C34.1, D15.1 (K), K2.2, R9.2, U14.5 (EN), U14.16 (Vdd), U17.3 (V+); also elsewhere on the board
/BMS_COCKPIT: RN21.3 (R3.1); also elsewhere on the board
/EXT_FAULT: U14.4; also elsewhere on the board
/IMD_COCKPIT: RN21.4 (R4.1); also elsewhere on the board
/IMD_FAULT: U14.12; also elsewhere on the board
/MCU/BMS_FAULT: U17.5 (+); also elsewhere on the board
/MCU/TS_ON: TP27.1, U17.7 (+); also elsewhere on the board
/Probing/BMS_LATCHED: RN23.4 (R4.1), TP25.1, U14.9, U17.9 (+); also elsewhere on the board
/Probing/EXT_LATCHED: RN23.2 (R2.1), TP32.1, U14.13; also elsewhere on the board
/Probing/IMD_LATCHED: RN23.3 (R3.1), TP26.1, U14.10, U17.11 (+); also elsewhere on the board
/Probing/SD_RELAY_D: D15.2 (A), K2.1, Q2.3 (D), TP24.1; also elsewhere on the board
/Probing/TS_ON: RN23.1 (R1.1), TP28.1, U17.1; also elsewhere on the board
/SD_IN: K2.3; also elsewhere on the board
/SD_OUT: K2.4; also elsewhere on the board
/SD_RESET: C33.1, R9.1, R38.2, SW2.1, U14.3, U14.7, U14.11; also elsewhere on the board
/Shutdown/BMS_FAULT: U14.6, U17.2
/Shutdown/VREF_1.5V: RN13.7 (R2.2), RN13.8 (R1.2), U17.4 (-), U17.6 (-)
GND: C32.2, C33.2, C34.2, Q15.2 (S), R38.1, RN13.2 (R2.1), RN24.1 (R1.1), RN24.2 (R2.1), RN24.3 (R3.1), RN24.4 (R4.1), SW2.2, U14.8 (Vss), U17.12 (V-); also elsewhere on the board
unnamed: Q2.1 (G), RN23.8 (R1.2), RN24.5 (R4.2)
unnamed: Q13.1 (G), RN23.7 (R2.2), RN24.6 (R3.2)
unnamed: Q13.2 (S), Q14.3 (D)
unnamed: Q2.2 (S), Q13.3 (D)
unnamed: Q14.1 (G), RN23.6 (R3.2), RN24.7 (R2.2)
unnamed: Q14.2 (S), Q15.3 (D)
unnamed: Q15.1 (G), RN23.5 (R4.2), RN24.8 (R1.2)
unnamed: RN21.5 (R4.2), U17.13
unnamed: RN21.6 (R3.2), U17.14

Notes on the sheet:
SHUTDOWN CONTROL
RESET BUTTON WITH PULLUP (100K) FOR AMS AND IMD FAULT WITH START DELAY OF 120ms (BECAUSE OF C=1uF AND VIH MIN OF 4044 is 8.4V AT VCC=12V)
LACTHING IC
Saves the fault status until reset from: BMS and IMD
normally: RESET HIGH _FAULT HIGH > _LATCHED HIGH fault: _FAULT FALLING > _LATCHED LOW (holding) resetting: _FAULT HIGH RESET FALLING > _LATCHED HIGH
DNP
COCKPIT LEDs

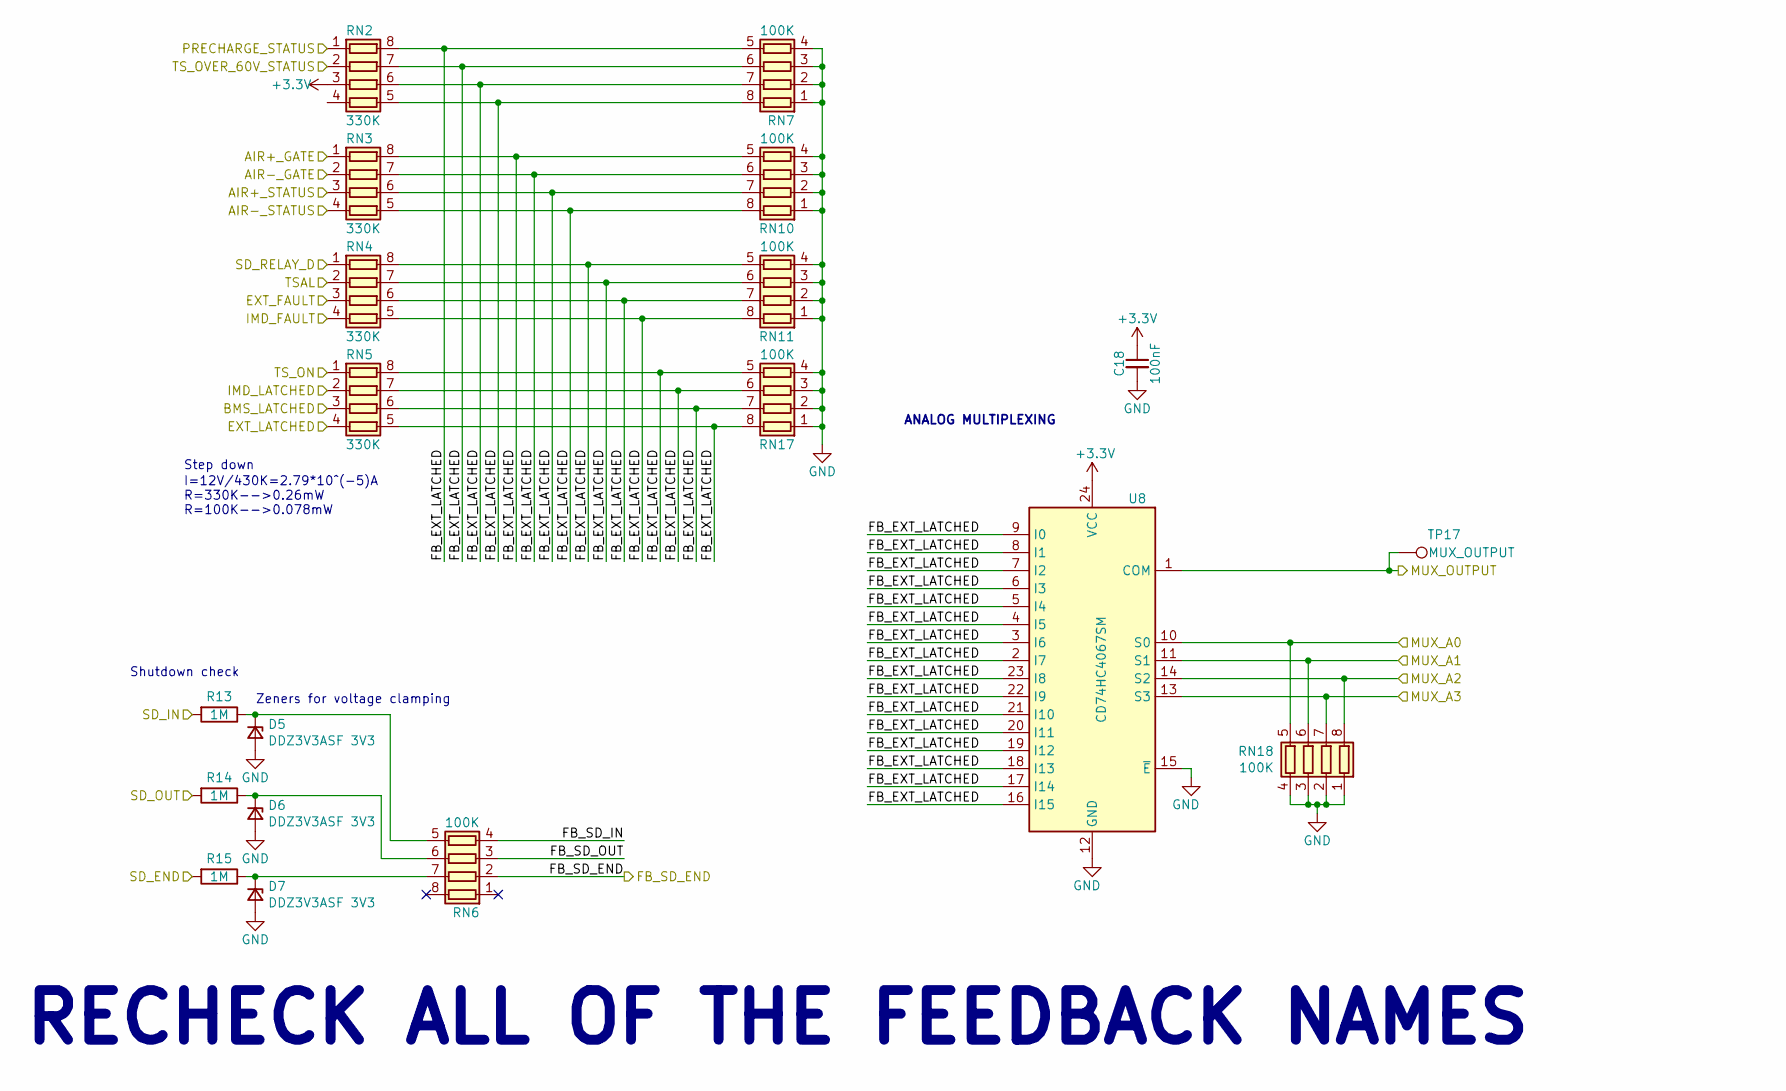
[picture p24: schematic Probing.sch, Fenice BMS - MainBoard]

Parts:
C18: 100nF; C_0603_1608Metric
D5, D6, D7: DDZ3V3ASF 3V3; D_SOD-323
R13, R14, R15: 1M; R_0603_1608Metric
RN2, RN3, RN4, RN5: 330K; R_Array_Convex_4x0603
RN6, RN7, RN10, RN11, RN17, RN18: 100K; R_Array_Convex_4x0603
TP17: MUX_OUTPUT; TestPoint_Pad_D1.0mm
U8: CD74HC4067SM; TSSOP-24_4.4x7.8mm_P0.65mm

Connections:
/AIRs/AIR+_GATE: RN3.1 (R1.1); also elsewhere on the board
/AIRs/AIR+_STATUS: RN3.3 (R3.1); also elsewhere on the board
/AIRs/AIR-_GATE: RN3.2 (R2.1); also elsewhere on the board
/AIRs/AIR-_STATUS: RN3.4 (R4.1); also elsewhere on the board
/EXT_FAULT: RN4.3 (R3.1); also elsewhere on the board
/HV/PRECHARGE_STATUS: RN2.1 (R1.1); also elsewhere on the board
/HV/TS_OVER_60V_STATUS: RN2.2 (R2.1); also elsewhere on the board
/IMD_FAULT: RN4.4 (R4.1); also elsewhere on the board
/MCU/FB_SD_END: RN6.2 (R2.1); also elsewhere on the board
/MCU/MUX_A0: RN18.5 (R4.2), U8.10 (S0)
/MCU/MUX_A1: RN18.6 (R3.2), U8.11 (S1)
/MCU/MUX_A2: RN18.8 (R1.2), U8.14 (S2)
/MCU/MUX_A3: RN18.7 (R2.2), U8.13 (S3)
/MCU/MUX_OUTPUT: TP17.1, U8.1 (COM); also elsewhere on the board
/Probing/BMS_LATCHED: RN5.3 (R3.1); also elsewhere on the board
/Probing/EXT_LATCHED: RN5.4 (R4.1); also elsewhere on the board
/Probing/FB_EXT_LATCHED: RN2.5 (R4.2), RN2.6 (R3.2), RN2.7 (R2.2), RN2.8 (R1.2), RN3.5 (R4.2), RN3.6 (R3.2), RN3.7 (R2.2), RN3.8 (R1.2), RN4.5 (R4.2), RN4.6 (R3.2), RN4.7 (R2.2), RN4.8 (R1.2), RN5.5 (R4.2), RN5.6 (R3.2), RN5.7 (R2.2), RN5.8 (R1.2), RN7.5 (R4.2), RN7.6 (R3.2), RN7.7 (R2.2), RN7.8 (R1.2), RN10.5 (R4.2), RN10.6 (R3.2), RN10.7 (R2.2), RN10.8 (R1.2), RN11.5 (R4.2), RN11.6 (R3.2), RN11.7 (R2.2), RN11.8 (R1.2), RN17.5 (R4.2), RN17.6 (R3.2), RN17.7 (R2.2), RN17.8 (R1.2), U8.2 (I7), U8.3 (I6), U8.4 (I5), U8.5 (I4), U8.6 (I3), U8.7 (I2), U8.8 (I1), U8.9 (I0), U8.16 (I15), U8.17 (I14), U8.18 (I13), U8.19 (I12), U8.20 (I11), U8.21 (I10), U8.22 (I9), U8.23 (I8)
/Probing/FB_SD_IN: RN6.4 (R4.1)
/Probing/FB_SD_OUT: RN6.3 (R3.1)
/Probing/IMD_LATCHED: RN5.2 (R2.1); also elsewhere on the board
/Probing/SD_RELAY_D: RN4.1 (R1.1); also elsewhere on the board
/Probing/TS_ON: RN5.1 (R1.1); also elsewhere on the board
/SD_END: R15.2; also elsewhere on the board
/SD_IN: R13.2; also elsewhere on the board
/SD_OUT: R14.2; also elsewhere on the board
/TSAL: RN4.2 (R2.1); also elsewhere on the board
GND: C18.2, D5.2 (A), D6.2 (A), D7.2 (A), RN7.1 (R1.1), RN7.2 (R2.1), RN7.3 (R3.1), RN7.4 (R4.1), RN10.1 (R1.1), RN10.2 (R2.1), RN10.3 (R3.1), RN10.4 (R4.1), RN11.1 (R1.1), RN11.2 (R2.1), RN11.3 (R3.1), RN11.4 (R4.1), RN17.1 (R1.1), RN17.2 (R2.1), RN17.3 (R3.1), RN17.4 (R4.1), RN18.1 (R1.1), RN18.2 (R2.1), RN18.3 (R3.1), RN18.4 (R4.1), U8.12 (GND), U8.15 (~E); also elsewhere on the board
unnamed: D5.1 (K), R13.1, RN6.5 (R4.2)
unnamed: D6.1 (K), R14.1, RN6.6 (R3.2)
unnamed: D7.1 (K), R15.1, RN6.7 (R2.2)

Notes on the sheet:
I=12V/430K=2.79*10^(-5)A R=330K-->0.26mW R=100K-->0.078mW
Step down
Zeners for voltage clamping
ANALOG MULTIPLEXING
RECHECK ALL OF THE FEEDBACK NAMES
Shutdown check

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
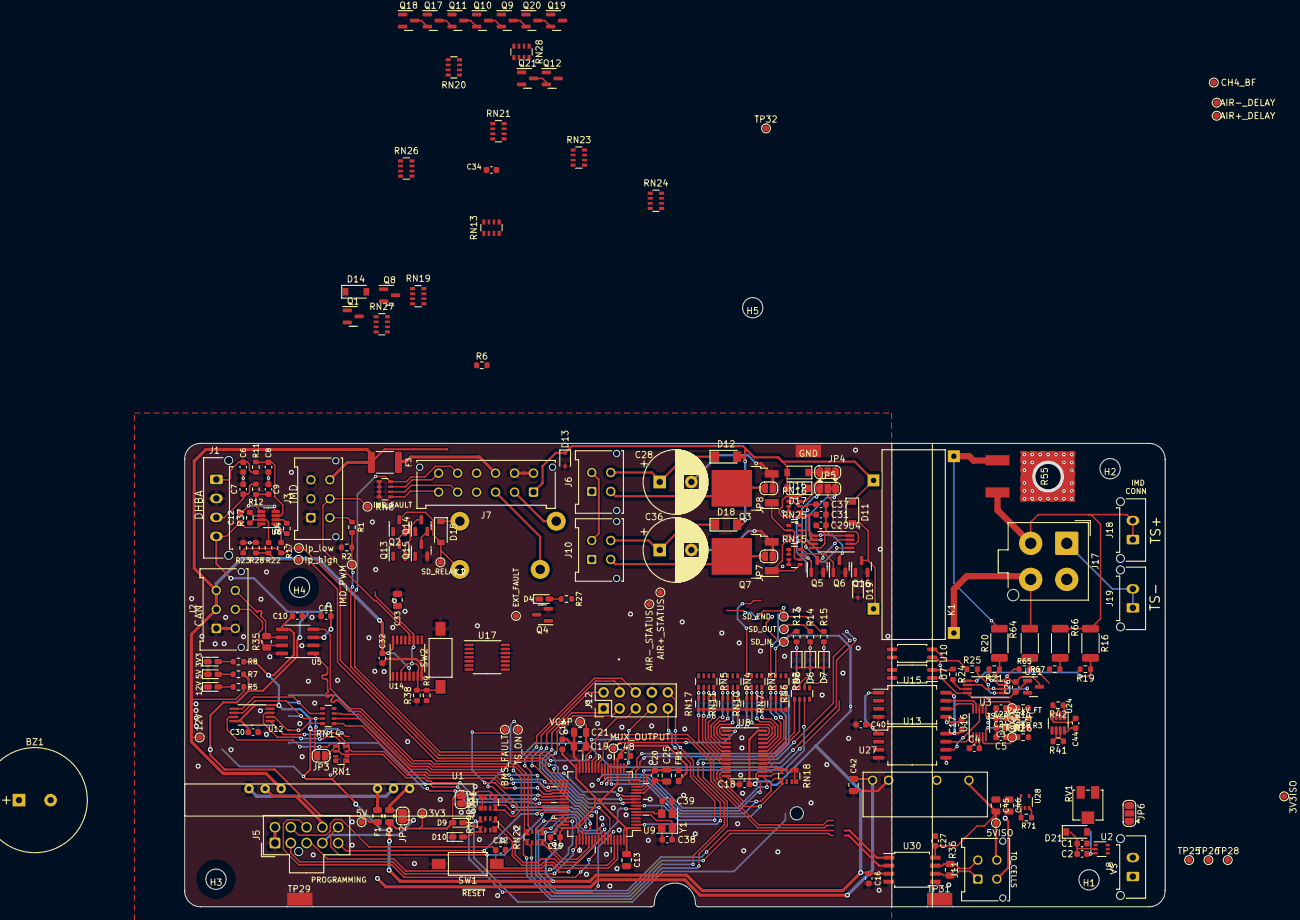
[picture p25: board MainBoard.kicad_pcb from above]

Board: 2 copper layers, 155.0 x 73.2 mm, 246 parts (1 on the bottom side), 199 nets.

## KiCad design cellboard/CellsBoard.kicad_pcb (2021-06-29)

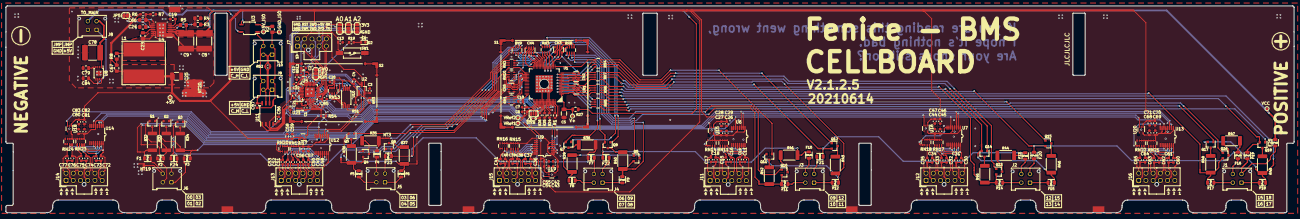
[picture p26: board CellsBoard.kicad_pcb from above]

Board: 2 copper layers, 445.5 x 71.5 mm, 275 parts (0 on the bottom side), 245 nets.

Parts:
C1, C11, C13, C14, C15, C16, C17, C18, C20, C21, C22, C26, C28, C30, C31, C32, C33, C34, C35, C36, C37, C38, C39, C40, C41, C42, C45, C47, C48, C49, C50, C51, C52, C53, C54, C57, C59, C60, C61, C62, C63, C64, C65, C69, C71, C72, C73, C74, C75, C76, C77, C81, C83, C85, C86, C87: 100nF; C_0603_1608Metric
C2, C3, C4, C6, C7, C10, C12, C27, C29, C43, C44, C46, C55, C56, C58, C68, C70, C80, C82: 1uF; C_0603_1608Metric
C5: 100nF_HV; C_1206_3216Metric
C8, C9, C78: 1u_HV; C_2220_5650Metric_Pad1.97x5.40mm_HandSolder
C19: 22n; C_0603_1608Metric_Pad1.08x0.95mm_HandSolder
C23, C66: 10n; C_0805_2012Metric_Pad1.18x1.45mm_HandSolder
C24: 1u; C_0805_2012Metric_Pad1.18x1.45mm_HandSolder
C25: 47u; C_1210_3225Metric_Pad1.33x2.70mm_HandSolder
C67: 3n; C_0805_2012Metric_Pad1.18x1.45mm_HandSolder
C79: 100n; C_0805_2012Metric
C84: 10n; C_0805_2012Metric
CN1, CN2, CN3, CN4, CN5: 10nF_array; C_4Array_1206
D2: LED_Small; D_0603_1608Metric
F1, F2, F3, F4, F5, F6, F7, F8, F9, F10, F11, F12, F13, F14, F15, F16, F17, F18, F19, F20, F21, F22, F23, F24, F25: Fuse; Fuse_0805
J1, J2, J3, J4, J5, J6: Conn_02x02_Odd_Even; Molex_Micro-Fit_3.0_43045-0412_2x02_P3.00mm_Vertical
J7: Conn_02x05_Top_Bottom; Molex_Nano-Fit_105310-xx10_2x05_P2.50mm_Vertical
J8: Conn_02x02_Counter_Clockwise; Molex_Micro-Fit_3.0_43045-0412_2x02_P3.00mm_Vertical
J9, J10: BUS; Molex_Micro-Fit_3.0_43045-0412_2x02_P3.00mm_Vertical
J11, J12, J13, J14, J15, J16: Conn_02x06_Top_Bottom; Molex_Nano-Fit_105310-xx12_2x06_P2.50mm_Vertical
JP1, JP2, JP3, JP4: SolderJumper_3_Open; SolderJumper-3_P1.3mm_Open_RoundedPad1.0x1.5mm
JP5: SolderJumper_2_Open; SolderJumper-2_P1.3mm_Open_RoundedPad1.0x1.5mm
JP20: DTEN; Jumper_adafruit
L1: 56u; sdr1307
NT0, NT1, NT2, NT3, NT4, NT5, NT6, NT7, NT8, NT9, NT10, NT11, NT12, NT13, NT14, NT15, NT16, NT17, NT18, NT19: Net-Tie_2; NetTie-2_SMD_Pad0.5mm
NT20: Net-Tie_2; NetTie-2_SMD_Pad2.0mm
Q1, Q2, Q3, Q4, Q5, Q6, Q7, Q8, Q9, Q10, Q11, Q12, Q13, Q14: TSM3401CX RFG; SOT-23
Q15, Q16, Q17, Q18: BSS308PE; SOT-23
R1: 100; R_0603_1608Metric
R2: 1.24k; R_0805_2012Metric_Pad1.20x1.40mm_HandSolder
R3: 100k; R_0805_2012Metric_Pad1.20x1.40mm_HandSolder
R4: 2k; R_0805_2012Metric_Pad1.20x1.40mm_HandSolder
R5: 215k; R_0805_2012Metric_Pad1.20x1.40mm_HandSolder
R6: 3k; R_0603_1608Metric_Pad0.98x0.95mm_HandSolder
R7: 2k; R_0603_1608Metric_Pad0.98x0.95mm_HandSolder
R8: 255k; R_0805_2012Metric_Pad1.20x1.40mm_HandSolder
R19: 3K3; R_0603_1608Metric
R24, R25: 1k; R_0603_1608Metric
R26: 1M; R_0603_1608Metric
R27: 100; R_0805_2012Metric
R32, R33, R34, R35, R36, R37, R38, R39, R40, R41, R42, R43, R44, R45, R46, R47, R48, R49: Rdsc; R_2512_6332Metric
R51: 1K; R_0603_1608Metric
R52: 150; R_0603_1608Metric
R53: 5K; R_0603_1608Metric
R54: 10K; R_0603_1608Metric
RN1, RN2, RN3, RN4, RN5: 3K3; R_Array_Convex_4x0603
RN6, RN7, RN8, RN9, RN10: 39; R_Array_Convex_4x0603
RN11, RN14, RN15, RN16, RN17, RN18, RN19, RN20, RN21, RN22, RN23, RN24: x; R_Array_Convex_4x0603
RN12: 1K; R_Array_Convex_2x0603
RN13: 1K; R_Array_Convex_4x0603
S1: RF_Shield_One_Piece; Harwin_shield_30x30mm_right_angle_clips
S2: RF_Shield_One_Piece; Harwin_shield_20x30mm_only_right_angle_clips
SW1: RESET; Button_SMD_6x3.5x4.3mm
TP1, TP2, TP3, TP4, TP7: TestPoint; TestPoint_GNDedge_toponly
TP5: VRef1; TestPoint_Pad_D1.0mm
TP6: VRef2; TestPoint_Pad_D1.0mm
TP8: V+; TestPoint_Pad_D1.0mm
TP9: +5V; TestPoint_Pad_D1.0mm
TP10: 5V_ISO; TestPoint_Pad_D1.0mm
TP11: GND_ISO; TestPoint_Pad_D1.0mm
TP12: VCC; TestPoint_Pad_D1.0mm
U1: LTC6813-1; LTC6813-1_minimal
U2: MCP1812; SOT-23_Handsoldering
U3: CPC1125N; SOP-4_3.8x4.1mm_P2.54mm
U4: LM5161PWP; HTSSOP-14-1EP_4.4x5mm_P0.65mm_EP3.4x5mm_Mask3x3.1mm
U5: STM32L432KBUx; QFN-32-1EP_5x5mm_P0.5mm_EP3.45x3.45mm
U6, U7, U9, U12, U13, U14: ADC128D818; TSSOP-16_4.4x5mm_P0.65mm
U8: MAQ5281; MSOP-8-1EP_3x3mm_P0.65mm_EP1.68x1.88mm
U10: M95256-W; TSSOP-8_4.4x3mm_P0.65mm
U11: MAX14878AWA+; SOIC-8_5.23x5.23mm_P1.27mm
U15, U16, U17, U18, U19, U20: MCP1811AT-033LT; SOT-353_SC-70-5
U21: DSC61XX; 4-Lead_CDFN_2.5x2.0mm

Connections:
+3V3: C1.2, C2.1, C4.1, C12.1, C20.2, C21.1, C22.1, C85.1, C86.2, J7.4, JP1.3, JP3.3, JP4.3, R51.2, R53.1, R54.2, RN12.1, RN12.2, RN13.2, RN13.3, RN13.4, U2.1, U5.1, U5.5, U5.17, U10.8, U11.3, U21.1, U21.4
+5V: C3.1, C10.1, C25.2, C28.2, C29.2, C46.2, C47.2, C54.2, C55.2, C58.2, C59.2, C67.2, C70.2, C71.2, C82.2, C83.2, J7.9, JP20.1, L1.2, R6.1, R26.2, TP9.1, U1.48, U2.2, U15.1, U16.1, U17.1, U18.1, U19.1, U20.1
/BATTERY MANAGER/C0: CN5.3, CN5.7, RN10.6, U1.38
/BATTERY MANAGER/C1: CN5.4, CN5.6, RN10.7, U1.36
/BATTERY MANAGER/C2: CN4.1, CN5.5, RN10.8, U1.34
/BATTERY MANAGER/C3: CN4.2, CN4.8, RN9.5, U1.32
/BATTERY MANAGER/C4: CN4.3, CN4.7, RN9.6, U1.30
/BATTERY MANAGER/C5: CN4.4, CN4.6, RN9.7, U1.28
/BATTERY MANAGER/C6: CN3.1, CN4.5, RN9.8, U1.26
/BATTERY MANAGER/C7: CN3.2, CN3.8, RN8.5, U1.24
/BATTERY MANAGER/C8: CN3.3, CN3.7, RN8.6, U1.22
/BATTERY MANAGER/C9: CN3.4, CN3.6, RN8.7, U1.20
/BATTERY MANAGER/C10: CN2.1, CN3.5, RN8.8, U1.18
/BATTERY MANAGER/C11: CN2.2, CN2.8, RN7.5, U1.16
/BATTERY MANAGER/C12: CN2.3, CN2.7, RN7.6, U1.14
/BATTERY MANAGER/C13: CN2.4, CN2.6, RN7.7, U1.12
/BATTERY MANAGER/C14: CN1.1, CN2.5, RN7.8, U1.10
/BATTERY MANAGER/C15: CN1.2, CN1.8, RN6.5, U1.8
/BATTERY MANAGER/C16: CN1.3, CN1.7, RN6.6, U1.6
/BATTERY MANAGER/C17: CN1.4, CN1.6, RN6.7, U1.4
/BATTERY MANAGER/C18: CN1.5, RN6.8, U1.2
/BATTERY MANAGER/CB0: NT0.2, RN10.3
/BATTERY MANAGER/CB1: NT1.2, RN10.2
/BATTERY MANAGER/CB2: NT2.2, RN10.1
/BATTERY MANAGER/CB3: NT3.2, RN9.4
/BATTERY MANAGER/CB4: NT4.2, RN9.3
/BATTERY MANAGER/CB5: NT5.2, RN9.2
/BATTERY MANAGER/CB6: NT6.2, RN9.1
/BATTERY MANAGER/CB7: NT7.2, RN8.4
/BATTERY MANAGER/CB8: NT8.2, RN8.3
/BATTERY MANAGER/CB9: NT9.2, RN8.2
/BATTERY MANAGER/CB10: NT10.2, RN8.1
/BATTERY MANAGER/CB11: NT11.2, RN7.4
/BATTERY MANAGER/CB12: NT12.2, RN7.3
/BATTERY MANAGER/CB13: NT13.2, RN7.2
/BATTERY MANAGER/CB14: NT14.2, RN7.1
/BATTERY MANAGER/CB15: NT15.2, RN6.4
/BATTERY MANAGER/CB16: NT16.2, RN6.3
/BATTERY MANAGER/CB17: NT17.2, RN6.2
/BATTERY MANAGER/CB18: NT18.2, RN6.1
/BATTERY MANAGER/CLK: U1.62, U5.11
/BATTERY MANAGER/IBIAS: R25.1, U1.57
/BATTERY MANAGER/ICMP: R24.2, R25.2, U1.58
/BATTERY MANAGER/MISO: R53.2, U1.54, U5.12
/BATTERY MANAGER/MOSI: U1.53, U5.13
/BATTERY MANAGER/V+: C5.1, R27.1, TP8.1, U1.1
/BATTERY MANAGER/VRef1: C6.1, TP5.1, U1.51
/BATTERY MANAGER/VRef2: C7.1, TP6.1, U1.50
/BATTERY MANAGER/WDT: R26.1, U1.56
/CB0: F1.2, NT0.1, R32.1
/CB0N: F1.1, J6.4, NT19.1
/CB1: F2.2, NT1.1, Q1.2, R33.1
/CB1N: F2.1, J6.2
/CB2: F3.2, NT2.1, Q2.2, R34.1
/CB2N: F3.1, J6.1
/CB3: F4.2, F24.2, NT3.1, Q3.2, R35.1
/CB3N-1: F4.1, J5.4
/CB3N-2: F24.1, J6.3
/CB4: F5.2, NT4.1, Q4.2, R36.1
/CB4N: F5.1, J5.2
/CB5: F6.2, NT5.1, Q5.2, R37.1
/CB5N: F6.1, J5.1
/CB6: F7.2, F23.2, NT6.1, Q6.2, R38.1
/CB6N-1: F7.1, J4.4
/CB6N-2: F23.1, J5.3
/CB7: F8.2, NT7.1, Q7.2, R39.1
/CB7N: F8.1, J4.2
/CB8: F9.2, NT8.1, Q8.2, R40.1
/CB8N: F9.1, J4.1
/CB9: F10.2, F22.2, NT9.1, Q9.2, R41.1
/CB9N-1: F22.1, J4.3
/CB9N-2: F10.1, J3.4
/CB10: F11.2, NT10.1, Q10.2, R42.1
/CB10N: F11.1, J3.2
/CB11: F12.2, NT11.1, Q11.2, R43.1
/CB11N: F12.1, J3.1
/CB12: F13.2, F21.2, NT12.1, Q12.2, R44.1
/CB12N-1: F13.1, J2.4
/CB12N-2: F21.1, J3.3
/CB13: F14.2, NT13.1, Q13.2, R45.1
/CB13N: F14.1, J2.2
/CB14: F15.2, NT14.1, Q14.2, R46.1
/CB14N: F15.1, J2.1
/CB15: F16.2, F20.2, NT15.1, Q15.2, R47.1
/CB15N-1: F16.1, J1.4
/CB15N-2: F20.1, J2.3
/CB16: F17.2, NT16.1, Q16.2, R48.1
/CB16N: F17.1, J1.2
/CB17: F18.2, NT17.1, Q17.2, R49.1
/CB17N: F18.1, J1.1
/CB18: F19.2, NT18.1, Q18.2
/CB18N: F19.1, F25.1, J1.3
/DCDC_80Vto5V/5V_ISO: C87.2, J9.4, J10.4, TP10.1, U3.1, U11.8
/DCDC_80Vto5V/120V_linreg: C78.2, J8.3, U8.1
/DCDC_80Vto5V/EN-D: R3.1, R4.2, U4.4
/DCDC_80Vto5V/EN-DCDC1: R3.2, U3.4
/DCDC_80Vto5V/FB-D: C66.1, R6.2, R7.1, U4.9
/DCDC_80Vto5V/GND_ISO: C87.1, J9.3, J10.3, R2.2, TP11.1, U11.5
/DCDC_80Vto5V/GND_SUPPLY: C8.1, C9.1, C19.1, C24.1, C25.1, C78.1, C79.2, C84.2, J8.2, NT20.1, R4.1, R7.2, TP7.1, U4.1, U4.2, U4.15, U8.5, U8.9
/DCDC_80Vto5V/SS-D: C19.2, U4.6
/DCDC_80Vto5V/SW-D: C23.1, L1.1, R8.2, U4.12, U4.13, U4.14
/DCDC_80Vto5V/VCC-D: C24.2, JP5.2, U4.10
/MOS_Balancer_Passive_metod/DIS_1: Q1.3, R32.2
/MOS_Balancer_Passive_metod/DIS_2: Q2.3, R33.2
/MOS_Balancer_Passive_metod/DIS_3: Q3.3, R34.2
/MOS_Balancer_Passive_metod/DIS_4: Q4.3, R35.2
/MOS_Balancer_Passive_metod/DIS_5: Q5.3, R36.2
/MOS_Balancer_Passive_metod/DIS_6: Q6.3, R37.2
/MOS_Balancer_Passive_metod/DIS_7: Q7.3, R38.2
/MOS_Balancer_Passive_metod/DIS_8: Q8.3, R39.2
/MOS_Balancer_Passive_metod/DIS_9: Q9.3, R40.2
/MOS_Balancer_Passive_metod/DIS_10: Q10.3, R41.2
/MOS_Balancer_Passive_metod/DIS_11: Q11.3, R42.2
/MOS_Balancer_Passive_metod/DIS_12: Q12.3, R43.2
/MOS_Balancer_Passive_metod/DIS_13: Q13.3, R44.2
/MOS_Balancer_Passive_metod/DIS_14: Q14.3, R45.2
/MOS_Balancer_Passive_metod/DIS_15: Q15.3, R46.2
/MOS_Balancer_Passive_metod/DIS_16: Q16.3, R47.2
/MOS_Balancer_Passive_metod/DIS_17: Q17.3, R48.2
/MOS_Balancer_Passive_metod/DIS_18: Q18.3, R49.2
/MOS_Balancer_Passive_metod/Q_S1: Q1.1, RN1.6
/MOS_Balancer_Passive_metod/Q_S2: Q2.1, RN1.5
/MOS_Balancer_Passive_metod/Q_S3: Q3.1, RN2.8
/MOS_Balancer_Passive_metod/Q_S4: Q4.1, RN2.7
/MOS_Balancer_Passive_metod/Q_S5: Q5.1, RN2.6
/MOS_Balancer_Passive_metod/Q_S6: Q6.1, RN2.5
/MOS_Balancer_Passive_metod/Q_S7: Q7.1, RN3.8
/MOS_Balancer_Passive_metod/Q_S8: Q8.1, RN3.7
/MOS_Balancer_Passive_metod/Q_S9: Q9.1, RN3.6
/MOS_Balancer_Passive_metod/Q_S10: Q10.1, RN3.5
/MOS_Balancer_Passive_metod/Q_S11: Q11.1, RN4.8
/MOS_Balancer_Passive_metod/Q_S12: Q12.1, RN4.7
/MOS_Balancer_Passive_metod/Q_S13: Q13.1, RN4.6
/MOS_Balancer_Passive_metod/Q_S14: Q14.1, RN4.5
/MOS_Balancer_Passive_metod/Q_S15: Q15.1, RN5.8
/MOS_Balancer_Passive_metod/Q_S16: Q16.1, RN5.7
/MOS_Balancer_Passive_metod/Q_S17: Q17.1, RN5.6
/MOS_Balancer_Passive_metod/Q_S18: Q18.1, RN5.5
/S1: RN1.3, U1.37
/S2: RN1.4, U1.35
/S3: RN2.1, U1.33
/S4: RN2.2, U1.31
/S5: RN2.3, U1.29
/S6: RN2.4, U1.27
/S7: RN3.1, U1.25
/S8: RN3.2, U1.23
/S9: RN3.3, U1.21
/S10: RN3.4, U1.19
/S11: RN4.1, U1.17
/S12: RN4.2, U1.15
/S13: RN4.3, U1.13
/S14: RN4.4, U1.11
/S15: RN5.1, U1.9
/S16: RN5.2, U1.7
/S17: RN5.3, U1.5
/S18: RN5.4, U1.3
/STM/ADC_nINT: R54.1, U5.18, U6.6, U7.6, U9.6, U12.6, U13.6, U14.6
/STM/ADD_0: JP1.2, U5.9
/STM/ADD_1: JP3.2, U5.8
/STM/ADD_2: JP4.2, U5.7
/STM/CANH_ISO: J9.2, J10.2, R52.1, U11.7
/STM/CANL_ISO: J9.1, J10.1, R52.2, U11.6
/STM/CAN_RX: U5.21, U11.1
/STM/CAN_TX: U5.22, U11.2
/STM/CS_EEPROM: RN13.5, U5.10, U10.1
/STM/MISO_EEPROM: RN13.6, U5.27, U10.2
/STM/MOSI_EEPROM: U5.28, U10.5
/STM/POWER_SENS_1: U5.3, U15.3, U16.3, U20.3
/STM/POWER_SENS_2: U5.2, U17.3, U18.3, U19.3
/STM/RESET: C13.1, J7.7, SW1.2, U5.4
/STM/RX: J7.10, U5.20
/STM/SCK_EEPROM: JP2.1, RN13.8, U10.6
/STM/SCL: RN12.4, U5.29, U6.3, U7.3, U9.3, U12.3, U13.3, U14.3
/STM/SDA: RN12.3, U5.30, U6.2, U7.2, U9.2, U12.2, U13.2, U14.2
/STM/SPI_CS: U1.61, U5.14
/STM/SWCLK: J7.2, U5.24
/STM/SWDIO: J7.3, U5.23
/STM/SWO: J7.8, JP2.3
/STM/TX: J7.5, U5.19
/STM/temperatureADC_0/3V3_SENS: C80.2, C81.2, RN23.1, RN23.2, RN23.3, RN23.4, RN24.1, RN24.2, RN24.3, U14.1, U14.5, U18.5
/STM/temperatureADC_0/MID: RN24.5, RN24.6
/STM/temperatureADC_1/3V3_SENS: C56.2, C57.2, RN19.1, RN19.2, RN19.3, RN19.4, RN20.1, RN20.2, RN20.3, U12.1, U12.5, U17.5
/STM/temperatureADC_1/A0: RN20.5, RN20.6, U12.7
/STM/temperatureADC_2/3V3_SENS: C42.2, C43.2, RN15.1, RN15.2, RN15.3, RN15.4, RN16.1, RN16.2, RN16.3, U9.1, U9.5, U9.7, U19.5
/STM/temperatureADC_2/MID: RN16.5, RN16.6
/STM/temperatureADC_3/3V3_SENS: C26.2, C27.2, RN11.1, RN11.2, RN11.3, RN11.4, RN14.1, RN14.2, RN14.3, U6.1, U6.5, U15.5
/STM/temperatureADC_3/A1: RN14.5, RN14.6, U6.8
/STM/temperatureADC_4/3V3_SENS: C44.2, C45.2, RN17.1, RN17.2, RN17.3, RN17.4, RN18.1, RN18.2, RN18.3, U7.1, U7.5, U16.5
/STM/temperatureADC_4/A0: RN18.5, RN18.6, U7.7, U7.8
/STM/temperatureADC_5/3V3_SENS: C68.2, C69.2, RN21.1, RN21.2, RN21.3, RN21.4, RN22.1, RN22.2, RN22.3, U13.1, U13.5, U13.7, U20.5
/STM/temperatureADC_5/A1: RN22.5, RN22.6, U13.8
/STM/~HOLD~: RN13.7, U5.15, U10.7
/STM/~W~: R51.1, U10.3
GND: C1.1, C2.2, C3.2, C4.2, C5.2, C6.2, C7.2, C10.2, C11.2, C12.2, C13.2, C14.2, C15.2, C16.2, C17.2, C18.2, C20.1, C21.2, C22.2, C26.1, C27.1, C28.1, C29.1, C30.2, C31.2, C32.2, C33.2, C34.2, C35.2, C36.2, C37.2, C38.2, C39.2, C40.2, C41.2, C42.1, C43.1, C44.1, C45.1, C46.1, C47.1, C48.2, C49.2, C50.2, C51.2, C52.2, C53.2, C54.1, C55.1, C56.1, C57.1, C58.1, C59.1, C60.2, C61.2, C62.2, C63.2, C64.2, C65.2, C68.1, C69.1, C70.1, C71.1, C72.2, C73.2, C74.2, C75.2, C76.2, C77.2, C80.1, C81.1, C82.1, C83.1, C85.2, C86.1, CN5.1, CN5.2, CN5.8, D2.1, J7.1, J7.6, J11.1, J11.2, J11.3, J11.4, J11.5, J11.6, J12.1, J12.2, J12.3, J12.4, J12.5, J12.6, J13.1, J13.2, J13.3, J13.4, J13.5, J13.6, J14.1, J14.2, J14.3, J14.4, J14.5, J14.6, J15.1, J15.2, J15.3, J15.4, J15.5, J15.6, J16.1, J16.2, J16.3, J16.4, J16.5, J16.6, JP1.1, JP3.1, JP4.1, JP20.3, NT19.2, NT20.2, R24.1, RN10.4, RN10.5, RN13.1, RN14.4, RN16.4, RN18.4, RN20.4, RN22.4, RN24.4, S1.1, S2.1, SW1.1, TP1.1, TP2.1, TP3.1, TP4.1, U1.55, U1.59, U1.60, U1.65, U2.3, U5.16, U5.31, U5.32, U5.33, U6.4, U6.7, U7.4, U9.4, U9.8, U10.4, U11.4, U12.4, U12.8, U13.4, U14.4, U14.7, U14.8, U15.2, U16.2, U17.2, U18.2, U19.2, U20.2, U21.2
unnamed: C11.1, J11.12, RN11.8, U6.16
unnamed: C14.1, J11.11, RN11.7, U6.15
unnamed: C15.1, J11.10, RN11.6, U6.14
unnamed: C16.1, J11.9, RN11.5, U6.13
unnamed: C17.1, J11.8, RN14.8, U6.12
unnamed: C18.1, J11.7, RN14.7, U6.11
unnamed: C23.2, U4.11
unnamed: C30.1, J12.12, RN17.8, U7.16
unnamed: C31.1, J12.11, RN17.7, U7.15
unnamed: C32.1, J12.10, RN17.6, U7.14
unnamed: C33.1, J12.9, RN17.5, U7.13
unnamed: C34.1, J12.8, RN18.8, U7.12
unnamed: C35.1, J12.7, RN18.7, U7.11
unnamed: C36.1, J15.12, RN15.8, U9.16
unnamed: C37.1, J15.11, RN15.7, U9.15
unnamed: C38.1, J15.10, RN15.6, U9.14
unnamed: C39.1, J15.9, RN15.5, U9.13
unnamed: C40.1, J15.8, RN16.8, U9.12
unnamed: C41.1, J15.7, RN16.7, U9.11
unnamed: C48.1, J13.12, RN19.8, U12.16
unnamed: C49.1, J13.11, RN19.7, U12.15
unnamed: C50.1, J13.10, RN19.6, U12.14
unnamed: C51.1, J13.9, RN19.5, U12.13
unnamed: C52.1, J13.8, RN20.8, U12.12
unnamed: C53.1, J13.7, RN20.7, U12.11
unnamed: C60.1, J16.12, RN21.8, U13.16
unnamed: C61.1, J16.11, RN21.7, U13.15
unnamed: C62.1, J16.10, RN21.6, U13.14
unnamed: C63.1, J16.9, RN21.5, U13.13
unnamed: C64.1, J16.8, RN22.8, U13.12
unnamed: C65.1, J16.7, RN22.7, U13.11
unnamed: C66.2, C67.1, R8.1
unnamed: C72.1, J14.12, RN23.8, U14.16
unnamed: C73.1, J14.11, RN23.7, U14.15
unnamed: C74.1, J14.10, RN23.6, U14.14
unnamed: C75.1, J14.9, RN23.5, U14.13
unnamed: C76.1, J14.8, RN24.8, U14.12
unnamed: C77.1, J14.7, RN24.7, U14.11
unnamed: C79.1, U8.4
unnamed: C84.1, J8.1, U8.6, U8.8
unnamed: D2.2, R19.2
unnamed: JP2.2, U5.26
unnamed: JP5.1, U4.8
unnamed: JP20.2, U1.52
unnamed: R1.1, U1.63
unnamed: R1.2, U1.64
unnamed: R2.1, U3.2
unnamed: R5.2, U4.5
unnamed: R19.1, U5.25
unnamed: U5.6, U21.3
VCC: C8.2, C9.2, F25.2, J8.4, R5.1, R27.2, TP12.1, U3.3, U4.3

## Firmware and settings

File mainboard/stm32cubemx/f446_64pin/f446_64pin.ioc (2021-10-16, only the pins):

Mcu.UserName=STM32F446RETx
PA0-WKUP.GPIO_Label=FB_RELAY_LV
PA0-WKUP.Signal=ADCx_IN0
PA1.GPIO_Label=FB_FROM_TSMS
PA1.Signal=ADCx_IN1
PA10.GPIO_Label=RX_SWD
PA10.Signal=USART1_RX
PA11.GPIO_Label=CAN_RX
PA11.Signal=CAN1_RX
PA12.GPIO_Label=CAN_TX
PA12.Signal=CAN1_TX
PA13.Signal=SYS_JTMS-SWDIO
PA14.Signal=SYS_JTCK-SWCLK
PA2.GPIO_Label=FB_IMD_FAULT
PA2.Signal=ADCx_IN2
PA3.Signal=ADCx_IN3
PA4.GPIO_Label=MUX_INPUT
PA4.Signal=ADCx_IN4
PA5.Signal=SPI1_SCK
PA6.Signal=SPI1_MISO
PA7.Signal=SPI1_MOSI
PA9.GPIO_Label=TX_SWD
PA9.Signal=USART1_TX
PB13.Signal=SPI2_SCK
PB14.Signal=SPI2_MISO
PB15.Signal=SPI2_MOSI
PB2.GPIO_Label=IMD_PWM
PB2.Signal=S_TIM2_CH4
PB3.Signal=SYS_JTDO-SWO
PB5.GPIO_Label=CAN_CELL_RX
PB5.Signal=CAN2_RX
PB6.GPIO_Label=CAN_CELL_TX
PB6.Signal=CAN2_TX
PB8.GPIO_Label=LED2
PB8.Signal=S_TIM4_CH3
PB9.GPIO_Label=LED1
PB9.Signal=S_TIM4_CH4
PC1.GPIO_Label=CHARGE
PC1.Signal=ADCx_IN11
PC10.GPIO_Label=BMS_FAULT
PC10.Signal=GPIO_Output
PC11.GPIO_Label=TS_ON
PC11.Signal=GPIO_Output
PC12.GPIO_Label=AIRP_OFF
PC12.Signal=GPIO_Output
PC2.GPIO_Label=IP_LOW
PC2.Signal=ADCx_IN12
PC3.GPIO_Label=IP_HIGH
PC3.Signal=ADCx_IN13
PC4.GPIO_Label=CS_ADC
PC4.Signal=GPIO_Output
PC6.GPIO_Label=CS_EEPROM
PC6.Signal=GPIO_Output
PC7.GPIO_Label=HOLD
PC7.Signal=GPIO_Output
PC8.GPIO_Label=CS_CARD
PC8.Signal=GPIO_Output
PC9.GPIO_Label=CARD_OK
PC9.Signal=GPIO_Input
PD2.GPIO_Label=AIRN_OFF
PD2.Signal=GPIO_Output
PH0-OSC_IN.Signal=RCC_OSC_IN
PH1-OSC_OUT.Signal=RCC_OSC_OUT

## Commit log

2020-10-15 First commit, git setup for kicad
2020-10-15 Converted to git, corrected a whole ton of rando symbols origins
    [HVSide.sch, MCU.sch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]
2020-10-16 added a lot of annotations and readability in the schematic, not complete
    [HVSide.sch, MCU.sch, MainBoard.kicad_pcb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]
2020-10-19 Logo wasn't virtual, new netlist
    [MainBoard.kicad_pcb]
2020-11-11 Updated the project to updates in the kicad libraries
    [MCU.sch]
2020-11-11 updated to new components as per v1.0.5
    [HVSide.sch, MCU.sch]
2020-11-11 Updated all to the last new v1.0.5 as printed by taba
    [MCU.sch, MainBoard.kicad_pcb, MainShutdown.sch]
2020-12-01 Board as soldered
    [MCU.sch]
2020-12-04 Moved mainboard stuff to its own folder
    [HVSide.sch, MCU.sch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]
2020-12-09 Added datasheet for STM32G4
2020-12-09 Corrected BOOT0
    [MCU.sch, MainBoard.kicad_pcb]
2020-12-10 Added jumper for BOOT0 to 3V3
    [MCU.sch, MainBoard.kicad_pcb]
2020-12-10 Added vias due to last boot0 modification
    [MainBoard.kicad_pcb]
2020-12-10 Added 64pin mcu and moved isocanspi to HV sheet
    [HVSide.sch, MCU.sch, MainBoard.sch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]
2020-12-23 added the stm32 configuration, neaten schematic
    [HVSide.sch]
2021-03-06 cellboard initial commit
    [Balance.sch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]
2021-03-06 excluding whole board step file
2021-03-06 general changes and comments, still WIP
    [HVSide.sch, MainBoard.kicad_pcb]
2021-03-06 adding output directory, ignore for librecad tempfiles
    [MainBoard-Edge_Cuts.dxf]
2021-03-06 removed rescue references and rescue library
    [CellsBoard.sch, LTC6813-1.sch, Temperature section.sch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]
2021-03-06 added version number, as printed
    [Balance.sch, CellsBoard.kicad_pcb, CellsBoard.sch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]
2021-03-07 64pin, testpoints, commenting, general refactoring
    [HVSide.sch, MCU.sch, MainBoard.sch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]
2021-03-11 renamed shutdown nets
    [MainBoard.sch, MainShutdown.sch]
2021-03-11 added image of shutdown path
    [MainBoard.sch, MainShutdown.sch]
2021-03-12 adding testpoints
    [HVSide.sch, MainBoard.sch, MainShutdown.sch]
2021-03-12 minor changes
    [HVSide.sch, MainShutdown.sch]
2021-03-12 changed Q2
    [MainShutdown.sch]
2021-03-13 redone the air connections for clarity
    [MainShutdown.sch]
2021-03-15 Redone the CD4072, it can't light a LED as per datasheet
    [HVSide.sch]
2021-03-27 added precharge rele suppression diode
    [MainShutdown.sch]
2021-03-27 commented AIR suppression
    [MainShutdown.sch]
2021-03-28 modifieed comment
    [MainShutdown.sch]
2021-04-21 updated libraries
    [MCU.sch]
2021-04-21 new standard connector
    [MainBoard.sch]
2021-06-22 v1.1 as printed
    [AIRs.sch, HVSide.sch, MCU.sch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]
2021-06-22 v2.1.2.5 as printed
    Commit on behalf of fran-retfie.
    [Balance.sch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]
2021-06-22 modified version number
    [Balance.sch, CellsBoard.kicad_pcb, CellsBoard.sch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]
2021-06-28 changed footprint mcp1811
    [CellsBoard.kicad_pcb, temperatureADC.sch]
2021-06-29 moved labels R5 C23
    [CellsBoard.kicad_pcb]
2021-07-28 Renamed handcart detection
    [AIRs.sch, HVSide.sch, MCU.sch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]
2021-10-16 Correction almost finished, Started layouting
    [AIRs.sch, HVSide.sch, MCU.sch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]
